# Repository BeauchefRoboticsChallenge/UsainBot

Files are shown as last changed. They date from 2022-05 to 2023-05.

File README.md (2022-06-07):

# UsainBot
[][cc-by-nc-sa]

UsainBot es un robot velocista del tipo seguidor de líneas cuyo objetivo es servir de referencia y plataforma para apoyar en la formación de los competidores. Está desarrollado en base a las tecnologías disponibles en un FabLab (impresión 3D, corte de PCBs, Arduino) y comprende las componentes más básicas para funcionar de acuerdo a las reglas de la competencia.

Un velocista seguidor de línea es un robot con ruedas que tiene la capacidad de distinguir franjas en una superficie de alto contraste (blanco y negro) y seguir su trayectoria de forma autónoma con la finalidad de completar un circuito lo más rápido posible.

# Diseño

## Antecedentes

Las funciones principales requeridas por el robot son:

- Reconocer franjas
- Movimiento
- Energía
- Procesamiento y control

Para esto requiere una construcción óptima en cuanto al tamaño/peso y las prestaciones de sus componentes que cumplirán estas funcionalidades, las cuales pueden ser desempeñadas por diferentes tipos y arreglos de sensores, motores, baterías, etc. Otras funciones secundarias corresponden a la interacción con el usuario (encender/apagar, activar, indicar acciones), así como cualquier otra que se desee agregar (como comunicación inalámbrica para el debugging).

En el contexto de la competencia, existirán marcadores a los costados del circuito que indicarán hitos como curvas, cruces y fin. También se fija el tamaño máximo como 25x25x20 centímetros (largo, ancho y alto) y que las ruedas no pueden contener elementos adherentes que dañen la pista.

(imagen de los hitos)

## Diseño original

UsainBot se diseñó considerando este set mínimo de subsistemas, las tecnologías disponibles en el Fablab U de Chile, la disponibilidad de componentes comerciales en el país (Chile) y otros diseños populares de robots velocistas. Los dibujos del sistema se realizaron en AutodeskFusion 360 y se llegó al siguiente diseño:

(vistas del usainbot)

### Sensores

UsainBot cuenta con un arreglo de sensores infrarrojos modelo asdasdasdsad en el frente. Esta disposición permite detectar con cierto nivel de resolución la desviación del eje central del robot respecto a la franja del circuito y tener un mejor control:

(esquema)

También posee dos sensores simples del mismo tipo (modelo sadads) en cada lado para la detección de franjas.

(imagen con zoom)

### Actuación

El robot posee una configuración diferencial, dos ruedas controladas por motores DC idénticos modelo asdasdsad, de x rpm nominales y v Volts.

La llanta de la rueda, impresa en 3D, posee una muesca donde se inserta el eje del motor (que tiene una muesca opuesta) a presión, mientras que el neumático es de silicona.

Los motores se apernan al chasis mediante soportes impresos en 3D.

Considerando la corriente que requieren estos motores elegimos utilizar como driver el puente H sadasdasdasd.

### Controlador

Decidimos utilizar un Arduino Nano por varias razones: Soporte de software, tamaño, lógica de 5V (compatible con el resto de componentes), disponibilidad, precio, facilidad de uso (cuenta con pines y puerto USB), entre otras.

### Batería

Considerando el voltaje necesario para el controlador y los motores, los cuales además suelen requerir altos niveles de corriente súbitamente es que elegimos utilizar una batería LiPo de 7.4 V modelo asdsdasad. Con tal capacidad permitirá realizar pruebas un par de horas antes de volver a cargarla sin conllevar mucho peso sobre el sistema.

### Chasis

Con el objetivo de minimizar el peso y tamaño se diseña una PCB con doble propósito: ubicar los componentes en el mínimo espacio posible y como chasis del robot, considerando que la placa de sadklsdajlkasdjlk tiene rigidez suficiente.

(imagen de la PCB)

La PCB tiene conectores para intercambiar fácilmente los componentes en caso de que sufran algún desperfecto, así como orificios para el montaje de los motores.

### Otros

Como tercer punto de apoyo se utiliza la parte cabeza de un LED redondo.

Utilizamos un buzzer standard de 5V para que el robot informe mediante alertas sonoras el estado en el que se encuentra.

Incluimos un switch para energizar los sistemas desde la batería y un pulsador para iniciar la rutina de carrera.

# Lista de partes y materiales

## Partes comerciales

Item                     | Cantidad
 ---------------------------   | --------------
Motor DC con reducción 6V x rpm | 2
Driver asdasd | 1
Sensor QTR-8A | 1
Sensor QTR-1A | 2
Arduino Nano | 1
Lipo 7.4V | 1
Pulsador | 1
Switch | 1
LED | 1
Buzzer | 1

Otros elementos necesarios para el desarrollo del robot pero no que son parte del mismo corresponden a: cargador de LiPo, alarma de carga de batería.

## Partes manufacturadas

Item                     | Cantidad
 ---------------------------   | ------------
Llantas | 2
Neumáticos | 2
Chasis PCB | 1

## Materiales

- pines, conectores,
- placa fr-4
- silicona epóxica 20-50 Shore A
- pernos m3x8 (4)
- tuerca m3 (4)

# Manufactura

## Componentes

### Llantas y neumáticos

Dado que tenemos acceso a una impresora de tipo SLA (Form2), decidimos fabricar las llantas con resina tenaz (Tough Resin) para soportar posibles golpes y el ajuste a presión sobre el eje, y moldes para los neumáticos con resina estándar translúcida (Clear Resin), pues de esta forma es fácil desprender la pieza moldeada del molde mismo y además permite observar la presencia de burbujas durante el procseo de curado.

El neumático se fabrica directamente sobre la llanta, como se muestra en el diagrama:

Para el proceso es necesario mezclar la silicona en partes iguales, revolver y degasificar rapidamente antes de que la silicona empiece a solidificarse.

### Anclajes de motor

Estos anclajes afirman el motor utilizando pernos M3x8 y tuercas M3, son impresos en FDM con PLA.

### PCB

Para la manufactura de la PCB contamos con una máquina LPKF modelo sadasdsda. Las herramientas que utilizamos para el corte son:

- sdaasd
- asdsd
- sadsdasadsda

Antes de empezar a soldar los componentes es importante probar la integridad de las pistas midiendo la conductividad con un multímetro, para evitar corto circuitos y circuitos abiertos.

Luego soldamos los pines, buzzer, pulsador, switch y LED de acuerdo al esquema.

## Ensamble

1.- Montar las ruedas en cada motor
2.- Montar los motores con sus anclajes sobre la PCB.
3.- Conectar Arduino Nano
4.- Conectar sensores laterales
5.- Conectar arreglo de sensores frontal.
6.- Conectar driver.
7.- Montar batería con un elástico y conectar.

# Software

## Pista de pruebas

Para hacer pruebas de funcionamiento resulta muy útil tener una pequeña pista de pruebas, esta la fabricamos con un trozo de melamina delgado de color negro y cinta aislante de x mm de ancho de color blanco.

(imagen de la pista)

## Pruebas de subsistemas

Una vez que el sistema está ensamblado, los componentes deben ser probados separadamente antes de hacer la integración final. Para esto generamos códigos sencillos para ejecutar en el robot y observar tanto su funcionamiento como la información que entrega el Arduino a través del monitor serial.

- Prueba de motores.
- Prueba de sensores principal.
- Prueba de sensores laterales.

(links a los codigos)

## Integración

## Calibración del PID

El funcionamiento óptimo del robot implica maximizar la velocidad manteniendo el robot moviéndose dentro de la franja y colineal con esta. Para esto es necesario encontrar una configuración óptima de los parámetros del PID.

### Calibración "manual"

De acuerdo al comportamiento observado en las pruebas, se pueden hacer las siguientes modificaciones:

## Licencia
[][cc-by-nc-sa]

Este trabajo esta publicado bajo la licencia [Creative Commons Attribution-NonCommercial-ShareAlike 4.0 International
License][cc-by-nc-sa].

Si deseas utilizar nuestro robot en tus proyectos o si te interesa vender las placas, contáctanos y conversemos :)

[cc-by-nc-sa]: https://creativecommons.org/licenses/by-nc-sa/4.0/
[cc-by-nc-sa-image]: https://i.creativecommons.org/l/by-nc-sa/4.0/88x31.png
[cc-by-nc-sa-shield]: https://img.shields.io/badge/License-CC%20BY%20NC%20SA%204.0-lightgrey.svg

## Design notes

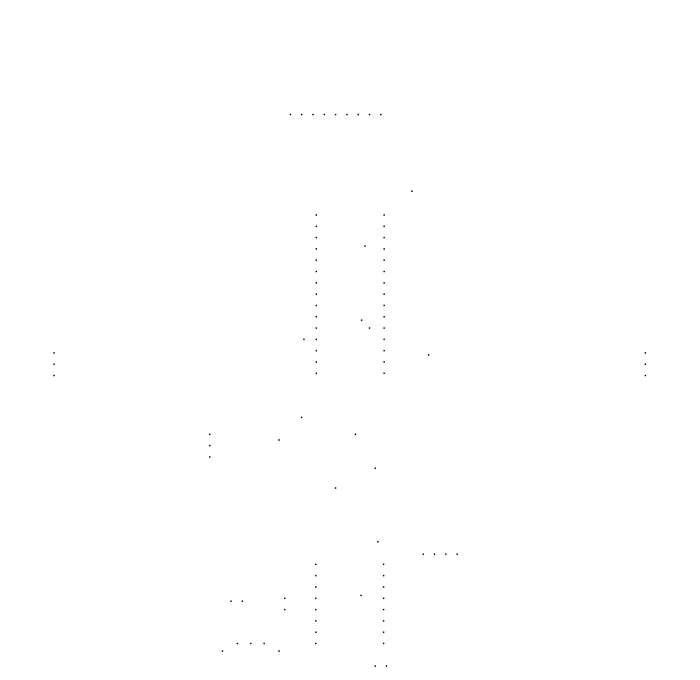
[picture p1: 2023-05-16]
pcb/usainbot2/usainv3_fabmod/drills.png

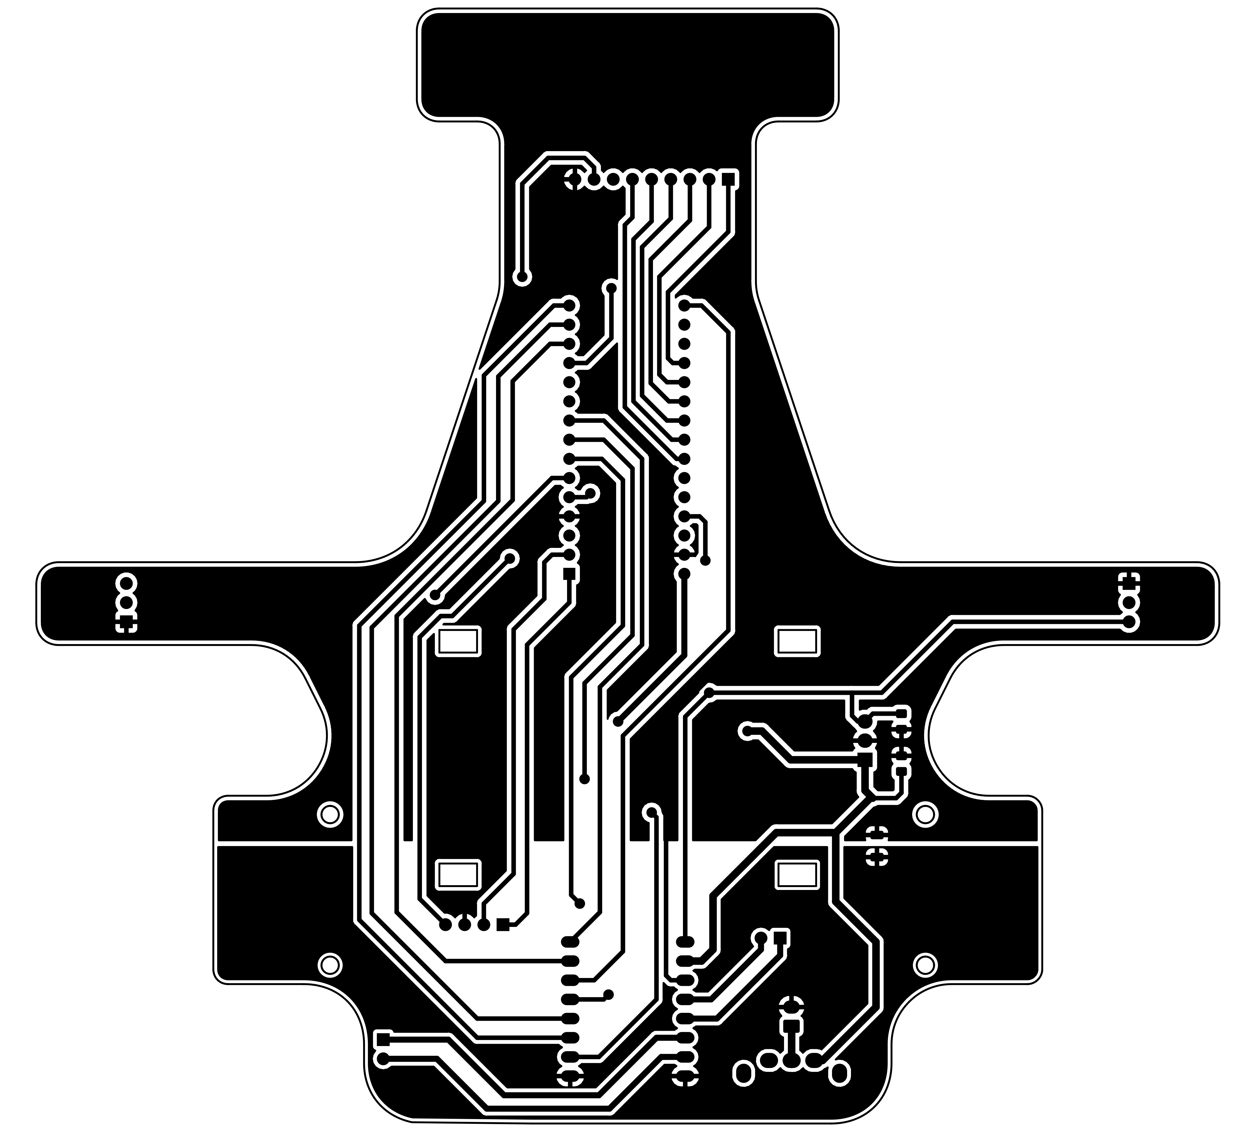
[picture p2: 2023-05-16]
pcb/usainbot2/brcito_fabmod/bot_inverted.png

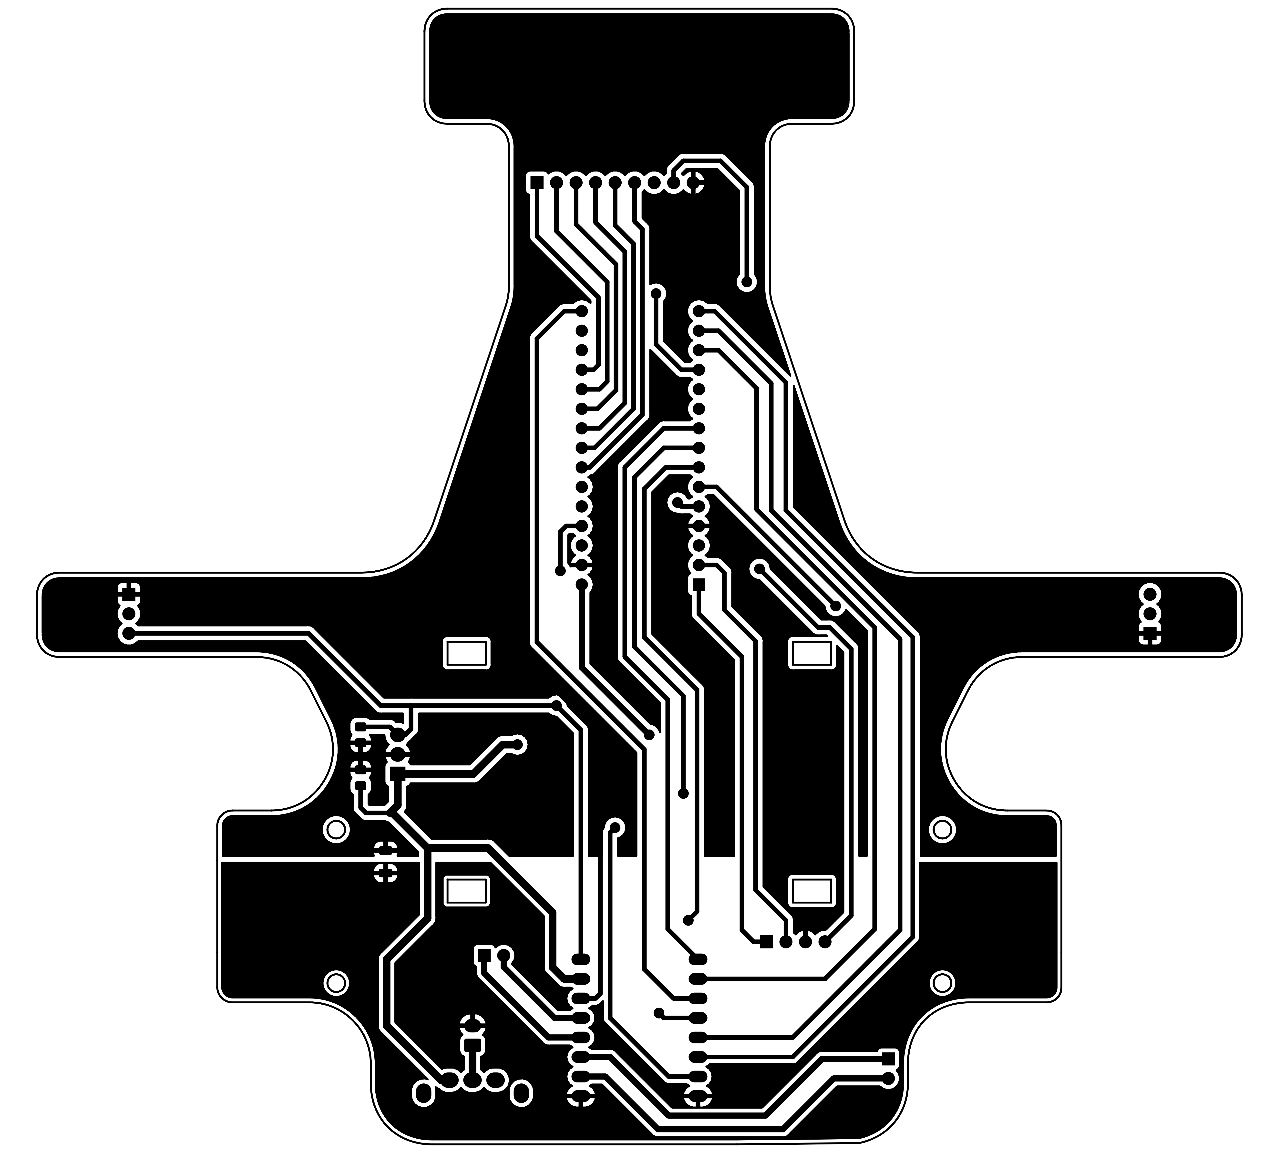
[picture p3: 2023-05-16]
pcb/usainbot2/brcito_fabmod/bot.png

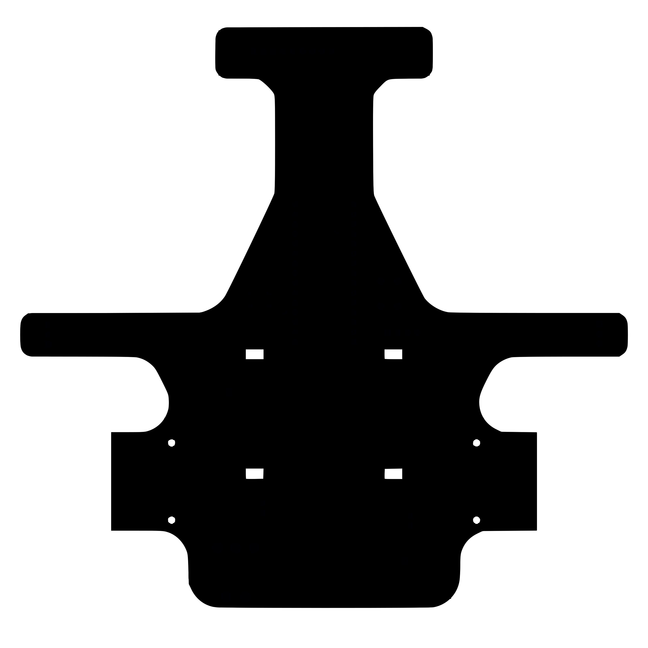
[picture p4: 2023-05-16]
pcb/usainbot2/contorno.png

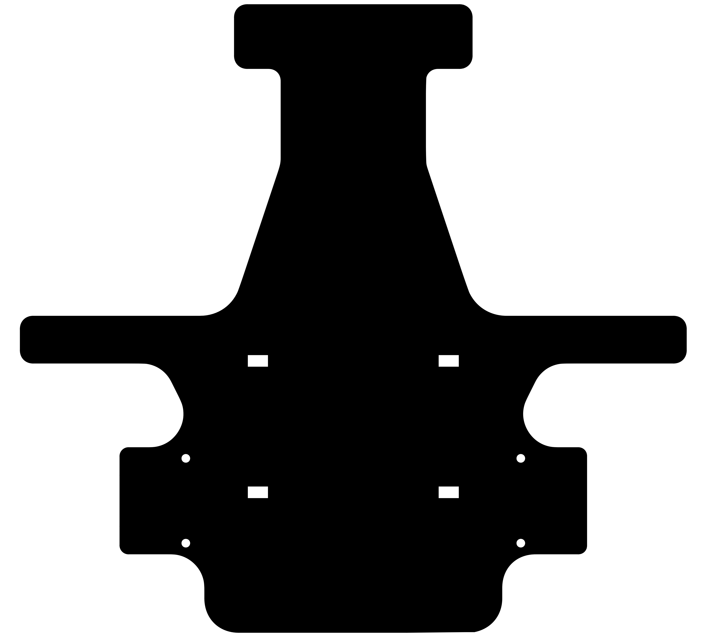
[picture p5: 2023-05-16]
pcb/usainbot2/brcito_fabmod/contorno.png

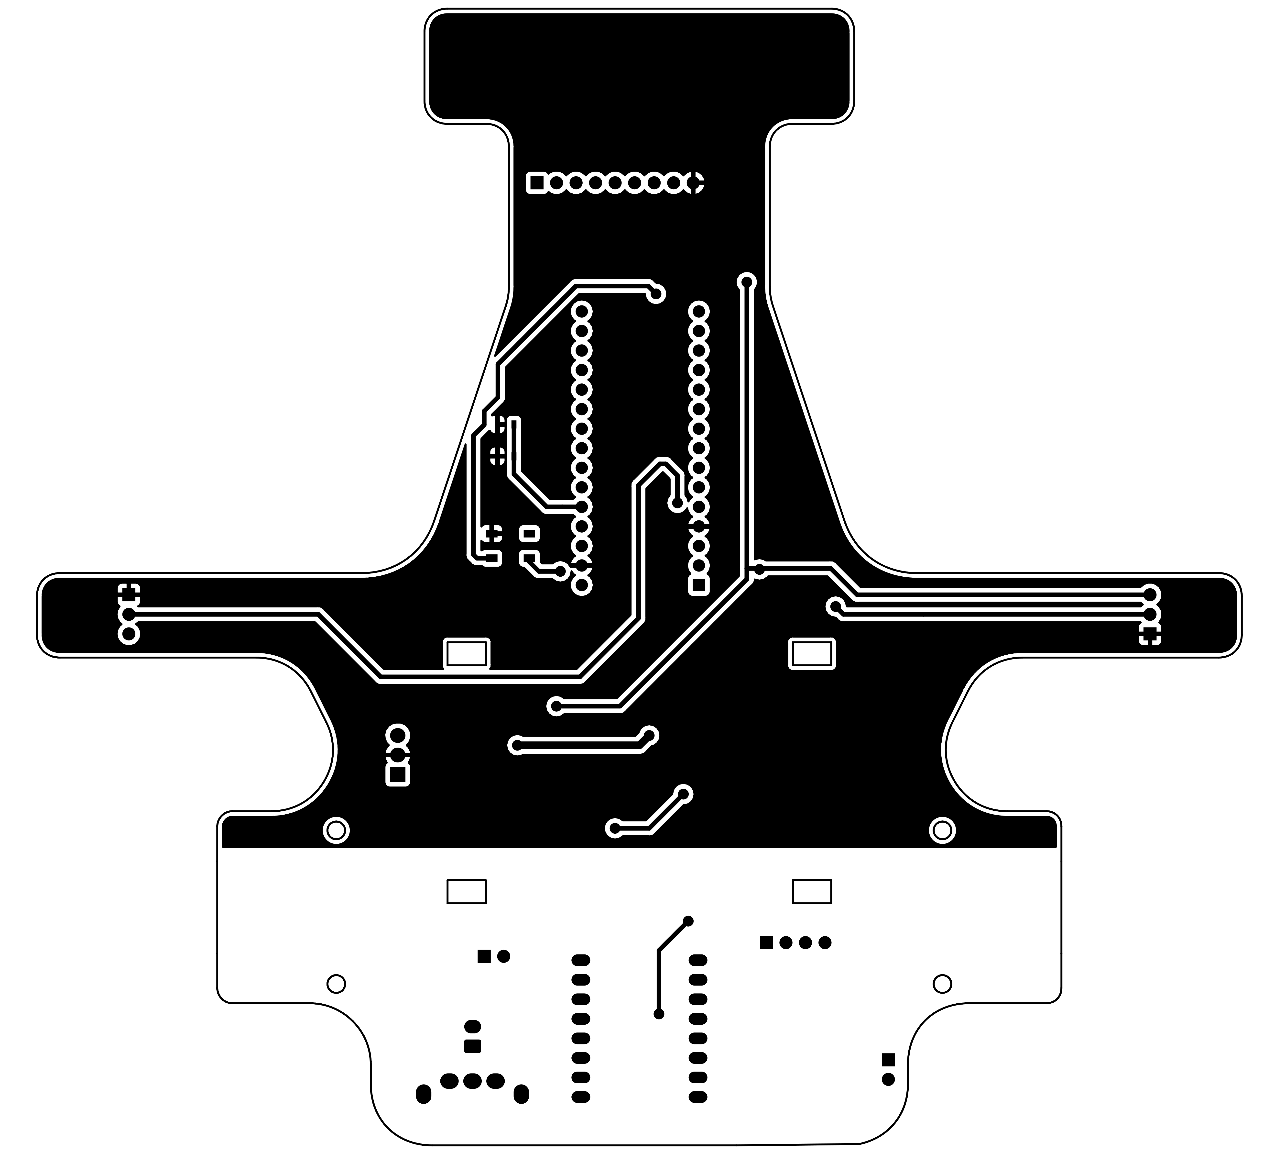
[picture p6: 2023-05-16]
pcb/usainbot2/brcito_fabmod/top.png

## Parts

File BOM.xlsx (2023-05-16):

Id | Designator | Package | Quantity | Designation | Supplier and ref
1 | U1 | TB6612FNG Breakout | 1 | TB6612FNG_breakout
 |  |  | 2 | pin socket 8x1
2 | J1 | PinSocket_1x04_P2.54mm_Vertical | 1 | BT_MOD
 |  |  | 1 | pin socket 4x1
3 | ArduinoNano1 | Arduino_Nano | 1 | Arduino_Nano_v3.x
 |  |  | 2 | pin socket 15x1
4 | C3,C2,C4 | C_0805_2012Metric_Pad1.18x1.45mm_HandSolder | 3 | 0.1u
5 | J5 | Molex_KK-254_AE-6410-06A_1x06_P2.54mm_Vertical | 1 | M1
6 | D1,D2 | LED_WS2812B_PLCC4_5.0x5.0mm_P3.2mm | 2 | WS2812B
7 | SW1 | SPST slide switch | 1 | SW_SPDT
8 | SW2 | SW_Push_1P1T_NO_Vertical_Wuerth_434133025816 | 1 | SW_Push
9 | U2 | TO-220-3_Vertical | 1 | LM7805_TO220
 |  |  | 1 | pin socket 3x1
10 | J7 | Molex_KK-254_AE-6410-06A_1x06_P2.54mm_Vertical | 1 | M2
11 | J6 | Molex_KK-254_AE-6410-02A_1x02_P2.54mm_Vertical | 1 | BATT
12 | J4 | PinHeader_1x09_P2.54mm_Horizontal | 1 | QTR-6A
13 | J3 | PinHeader_1x03_P2.54mm_Vertical | 1 | QTR1-R
14 | R0 | R_1206_3216Metric | 1 | RESISTOR1206
15 | J2 | PinHeader_1x03_P2.54mm_Vertical | 1 | QTR1-L
16 | R1 | R_1206_3216Metric_Pad1.30x1.75mm_HandSolder | 1 | 1K
17 | R2 | R_1206_3216Metric_Pad1.30x1.75mm_HandSolder | 1 | 2K
18 | C1 | C_0805_2012Metric_Pad1.18x1.45mm_HandSolder | 1 | 0.22u

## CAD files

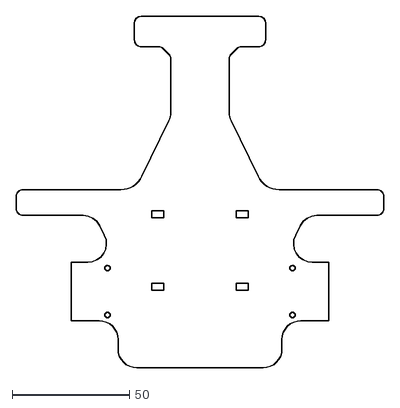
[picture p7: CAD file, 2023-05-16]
pcb/usainbot2/Maggibot_2022.dxf
157.0 x 150.0

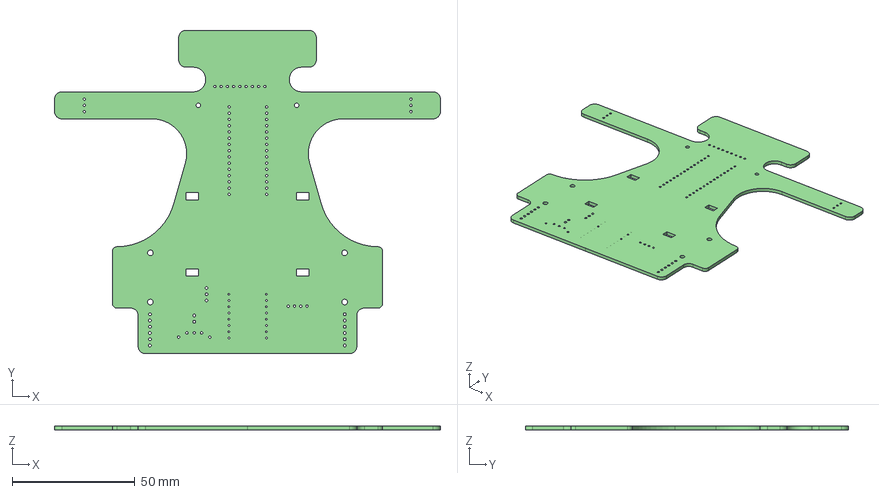
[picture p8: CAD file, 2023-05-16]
pcb/usainbot2/usainv3_fabmod/usainbot3.step
157.0 x 131.5 x 1.60 mm

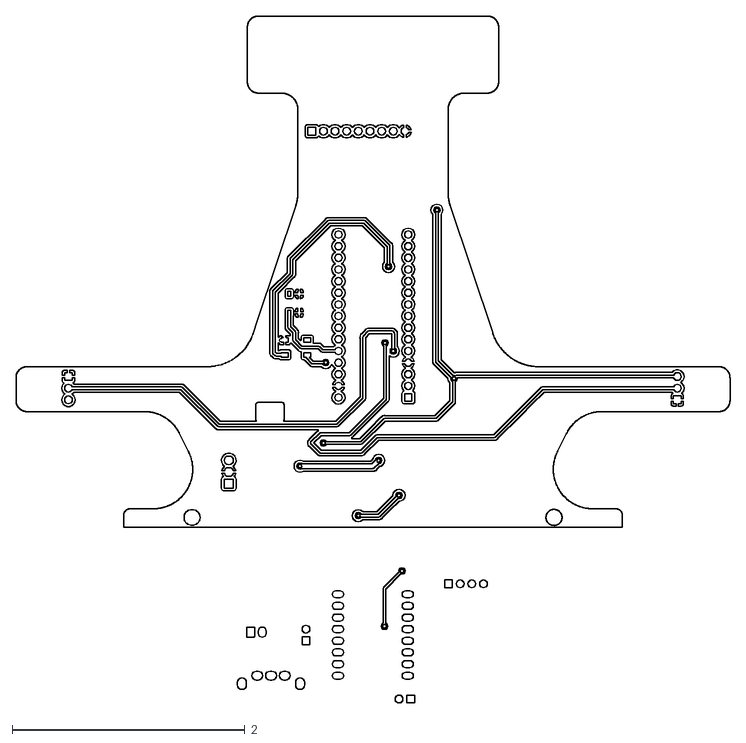
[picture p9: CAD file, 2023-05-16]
pcb/usainbot2/usainbot2-F_Cu.dxf
6.13 x 5.90

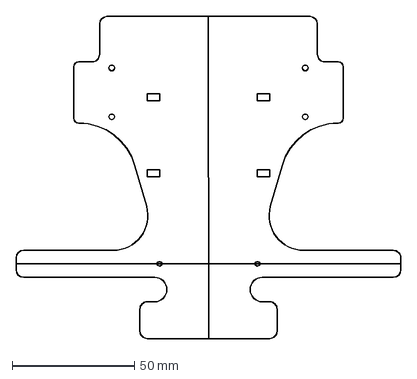
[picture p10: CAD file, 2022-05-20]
pcb/usainbot2/usainbot21_outline.dxf
157.0 x 131.5 mm

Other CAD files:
pcb/usainbot2/usainbot2.step

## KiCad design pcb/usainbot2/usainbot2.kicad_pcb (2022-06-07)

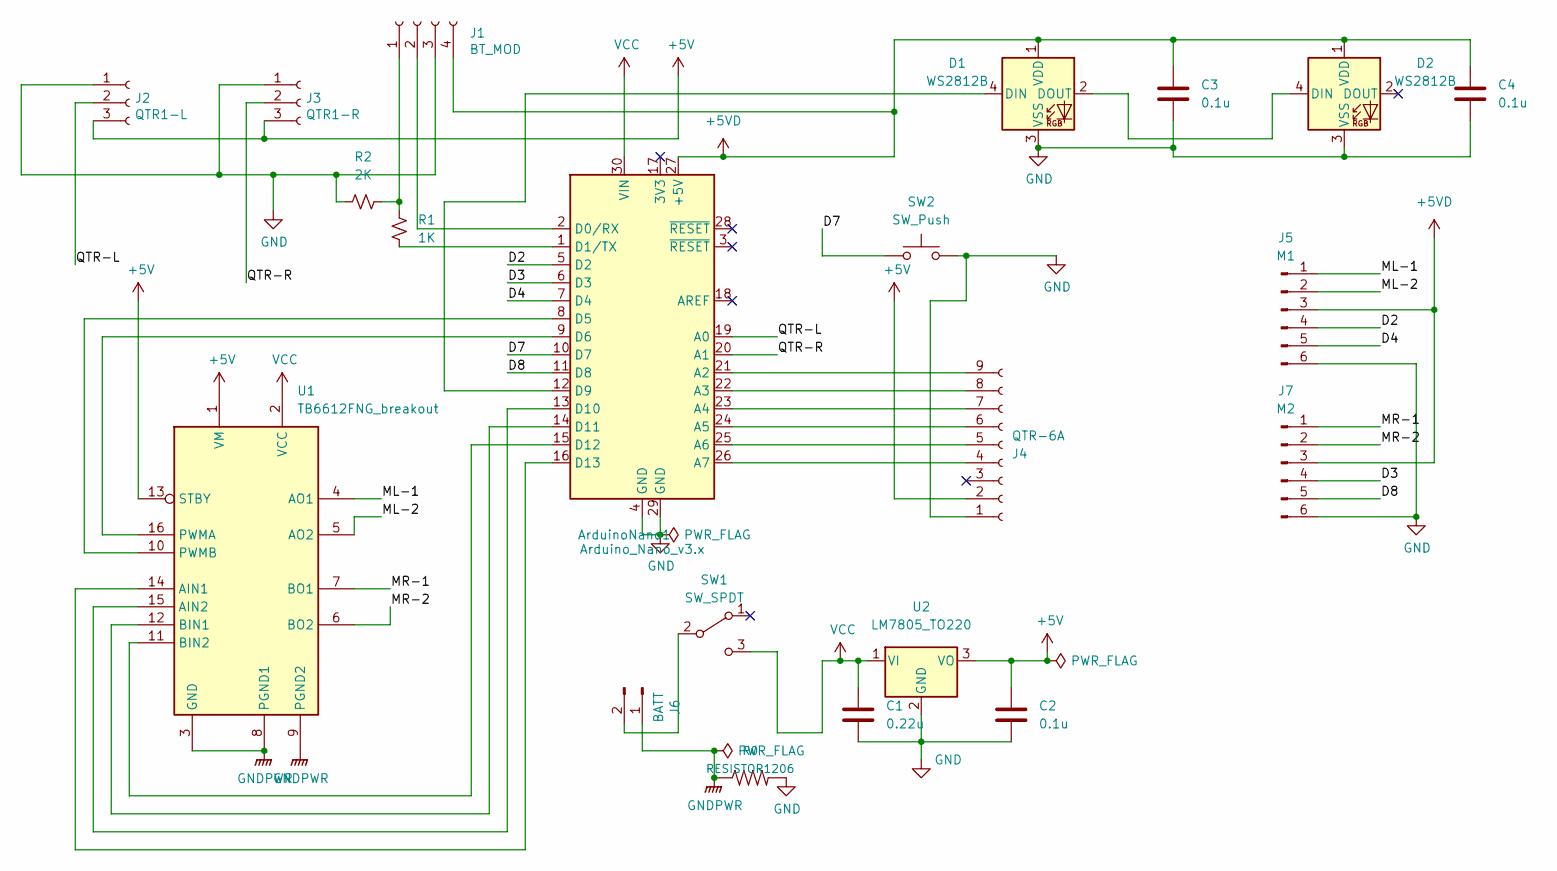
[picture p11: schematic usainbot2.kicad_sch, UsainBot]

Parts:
ArduinoNano1: Arduino_Nano_v3.x; Arduino_Nano
C1: 0.22u; C_0805_2012Metric_Pad1.18x1.45mm_HandSolder
C2, C3, C4: 0.1u; C_0805_2012Metric_Pad1.18x1.45mm_HandSolder
D1, D2: WS2812B; LED_WS2812B_PLCC4_5.0x5.0mm_P3.2mm
J1: BT_MOD; PinSocket_1x04_P2.54mm_Vertical
J2: QTR1-L; PinHeader_1x03_P2.54mm_Vertical
J3: QTR1-R; PinHeader_1x03_P2.54mm_Vertical
J4: QTR-6A; PinHeader_1x09_P2.54mm_Horizontal
J5: M1; Molex_KK-254_AE-6410-06A_1x06_P2.54mm_Vertical
J6: BATT; Molex_KK-254_AE-6410-02A_1x02_P2.54mm_Vertical
J7: M2; Molex_KK-254_AE-6410-06A_1x06_P2.54mm_Vertical
R0: RESISTOR1206; R_1206_3216Metric
R1: 1K; R_1206_3216Metric_Pad1.30x1.75mm_HandSolder
R2: 2K; R_1206_3216Metric_Pad1.30x1.75mm_HandSolder
SW1: SW_SPDT; SPST slide switch
SW2: SW_Push; SW_Push_1P1T_NO_Vertical_Wuerth_434133025816
U1: TB6612FNG_breakout; TB6612FNG Breakout
U2: LM7805_TO220; TO-220-3_Vertical

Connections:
+5V: C2.1, J2.3, J3.3, J4.2, U1.1 (VM), U1.13 (STBY), U2.3 (VO)
+5VD: ArduinoNano1.27 (+5V), C3.1, C4.1, D1.1 (VDD), D2.1 (VDD), J1.4, J5.3, J7.3
/D2: ArduinoNano1.5 (D2), J5.4
/D3: ArduinoNano1.6 (D3), J7.4
/D4: ArduinoNano1.7 (D4), J5.5
/D7: ArduinoNano1.10 (D7), SW2.1
/D8: ArduinoNano1.11 (D8), J7.5
/ML-1: J5.1, U1.4 (AO1)
/ML-2: J5.2, U1.5 (AO2)
/MR-1: J7.1, U1.7 (BO1)
/MR-2: J7.2, U1.6 (BO2)
/QTR-L: ArduinoNano1.19 (A0), J2.2
/QTR-R: ArduinoNano1.20 (A1), J3.2
GND: ArduinoNano1.4 (GND), ArduinoNano1.29 (GND), C1.2, C2.2, C3.2, C4.2, D1.3 (VSS), D2.3 (VSS), J1.3, J2.1, J3.1, J4.1, J5.6, J7.6, R0.2, R2.2, SW2.2, U2.2 (GND)
GNDPWR: J6.1, R0.1, U1.3 (GND), U1.8 (PGND1), U1.9 (PGND2)
unnamed: ArduinoNano1.1 (D1/TX), R1.2
unnamed: ArduinoNano1.2 (D0/RX), J1.2
unnamed: ArduinoNano1.8 (D5), U1.10 (PWMB)
unnamed: ArduinoNano1.9 (D6), U1.16 (PWMA)
unnamed: ArduinoNano1.12 (D9), D1.4 (DIN)
unnamed: ArduinoNano1.13 (D10), U1.15 (AIN2)
unnamed: ArduinoNano1.14 (D11), U1.12 (BIN1)
unnamed: ArduinoNano1.15 (D12), U1.11 (BIN2)
unnamed: ArduinoNano1.16 (D13), U1.14 (AIN1)
unnamed: ArduinoNano1.21 (A2), J4.9
unnamed: ArduinoNano1.22 (A3), J4.8
unnamed: ArduinoNano1.23 (A4), J4.7
unnamed: ArduinoNano1.24 (A5), J4.6
unnamed: ArduinoNano1.25 (A6), J4.5
unnamed: ArduinoNano1.26 (A7), J4.4
unnamed: D1.2 (DOUT), D2.4 (DIN)
unnamed: J1.1, R1.1, R2.1
unnamed: J6.2, SW1.2 (B)
VCC: ArduinoNano1.30 (VIN), C1.1, SW1.3 (C), U1.2 (VCC), U2.1 (VI)

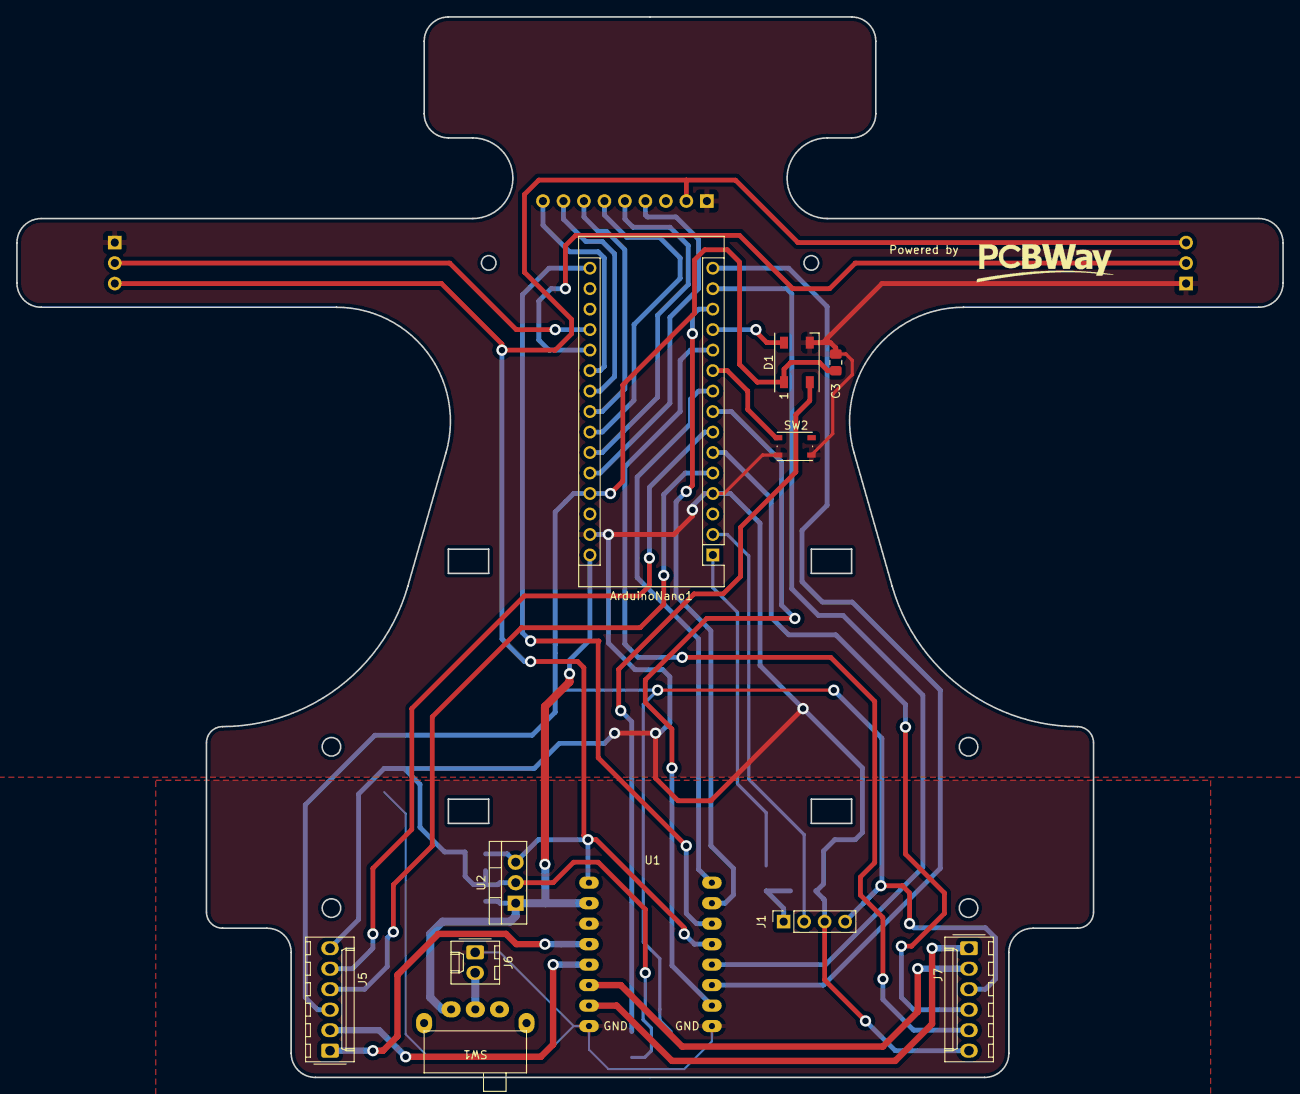
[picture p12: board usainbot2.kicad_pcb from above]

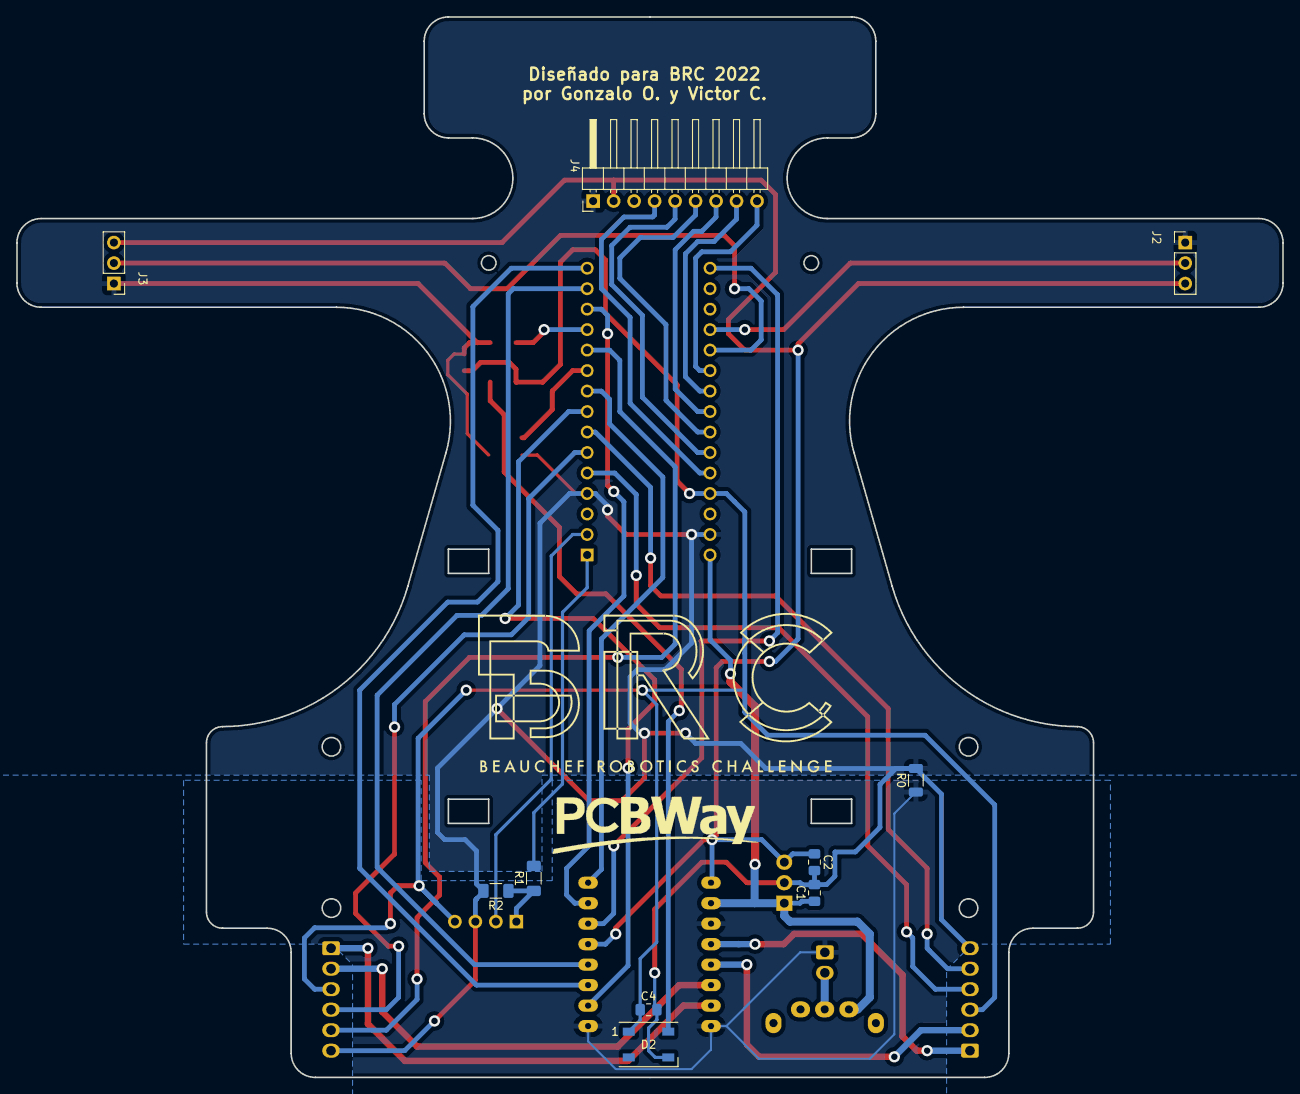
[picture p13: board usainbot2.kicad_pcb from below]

Board: 2 copper layers, 157.0 x 131.5 mm, 21 parts (10 on the bottom side), 34 nets.

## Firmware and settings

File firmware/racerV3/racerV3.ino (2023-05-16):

/* Sketch UsainBot v2.0

   by Gonzalo Olave based on v1.0 by Matias Mattamala and G.O.
   v1.0 -> https://github.com/mmattamala/racer/blob/master/arduino/robot_brc/robot_brc.ino
   last update 26/4/2022

   This code is in the public domain and it is licensed under the BEER-JUICE-WARE licence

   ------------------------------------------------------------
   "THE BEERWARE LICENSE" (Revision 42):
   The authors wrote this code. As long as you retain this
   notice, you can do whatever you want with this stuff. If we
   meet someday, and you think this stuff is worth it, you can
   buy us a beer in return (or a juice).
   ------------------------------------------------------------
*/

// debug
//#define DEBUG_SENSORS

#define CALIBRATE
// serial debug
#define DEBUG

#define LINE_WHITE

#include "DebugUtils.h"
#include <Adafruit_NeoPixel.h>
#include <QTRSensors.h>

// pinout del robot
#include "BRCito_defines.h"

// General definitions
#define LW 0  // left wheel
#define RW 1  // right wheel

#define TIMEOUT 2500

// Estos valores definen las velocidades de las ruedas
#define VEL_MIN 220
#define VEL_MAX 240        //130
#define VEL_CURVA_MAX 230  // 110
#define VEL_CURVA_MIN 0
#define MIN_ERR_THR 1000

// parámetros del controlador PID, para motores pololu de 1000rpm KP<1
float KP = 3;  // 0.3 //2
float KI = 0;
float KD = 15;  //5

// side sensor threshold
#define RS_TH 500
#define LS_TH 500

int r_sensor = 0;
int l_sensor = 0;
int r_counter = 0;
int l_counter = 0;
int st_sensor = 0;

float prop_err, int_err, der_err, last_err;
float pid_out;

bool stdby_state = 0;

// Variables will change:
int idleState = HIGH;       // the current state of the robot
int buttonState;            // the current reading from the input pin
int lastButtonState = LOW;  // the previous reading from the input pin

// the following variables are unsigned longs because the time, measured in
// milliseconds, will quickly become a bigger number than can be stored in an int.
unsigned long lastDebounceTime = 0;  // the last time the output pin was toggled
unsigned long debounceDelay = 50;    // the debounce time; increase if the output flickers

uint8_t lw_speed;
uint8_t rw_speed;

int th = 800;
float sum1 = 0;
float sum = 0;
float err = 0;
int s_min = TIMEOUT;
int s_max = 0;
float pos = 0;

int counter = 0;
int btn = 0;

uint16_t sensorSide[NUM_SIDE_SENSORS];
uint16_t sensorLine[NUM_ARRAY_SENSORS];

Adafruit_NeoPixel pixel = Adafruit_NeoPixel(2, LED_PIN, NEO_GRB + NEO_KHZ800);
QTRSensors qtr_line, qtr_side;

uint32_t BLACK = pixel.Color(0, 0, 0);
uint32_t RED = pixel.Color(255, 0, 0);        // rojo
uint32_t GREEN = pixel.Color(0, 255, 0);      // magenta
uint32_t BLUE = pixel.Color(0, 0, 200);       // magenta
uint32_t MAGENTA = pixel.Color(255, 0, 200);  // magenta
uint32_t YELLOW = pixel.Color(255, 140, 0);   // magenta
uint32_t ORANGE = pixel.Color(255, 50, 0);    // magenta
uint32_t CYAN = pixel.Color(0, 140, 200);     // cyan

int state = STDBY;

//-------------------------------
// Setup functions
//-------------------------------
void setupWheels() {

  // configure left wheel
  pinMode(PIN_LW_PWM, OUTPUT);
  pinMode(PIN_LW_A, OUTPUT);
  pinMode(PIN_LW_B, OUTPUT);

  // configure right wheel
  pinMode(PIN_RW_PWM, OUTPUT);
  pinMode(PIN_RW_A, OUTPUT);
  pinMode(PIN_RW_B, OUTPUT);

  onWheels();
}

void setupHW() {
  pinMode(BUTTON_PIN, INPUT_PULLUP);
}

void setupLeds() {
  pixel.begin();
}

void setupSensors() {
  qtr_side.setTypeRC();
  qtr_side.setSensorPins((const uint8_t[]){
                           PIN_LS, PIN_RS },
                         NUM_SIDE_SENSORS);
  qtr_line.setTypeAnalog();
  qtr_line.setSensorPins((const uint8_t[]){
    S1, S2, S3, S4, S5, S6}, NUM_ARRAY_SENSORS);

#ifdef CALIBRATE
  pixel.setPixelColor(LED_UP, RED);
  pixel.show();
  DEBUG_PRINT("Calibrando...");
  for (int i = 0; i < 100; i++)  // make the calibration take about 10 seconds
  {
    qtr_line.calibrate();
    qtr_side.calibrate();
  }
  pixel.setPixelColor(0, BLACK);
  pixel.show();
  DEBUG_PRINTLN("ok");
#endif
}

void setup() {

  Serial.begin(115200);  // for BT communication and debug

  setupWheels();
  setupLeds();
  setupHW();
  setupSensors();

  delay(500);

  pixel.setBrightness(100);
  pixel.setPixelColor(LED_UP, YELLOW);
  pixel.show();
  delay(500);

  while (true) {
    int boton = digitalRead(BUTTON_PIN);
    if (boton == 0) break;
  }
  delay(100);

  pixel.setPixelColor(LED_UP, GREEN);
  pixel.show();

  pixel.setPixelColor(LED_DOWN, BLUE);
  pixel.show();
  state = FOLLOW_LINE;
}

void loop() {
  // Step 1: Read Raw Sensors
  readRawSensors();

  //testBlink();
  /*
    testWheel(RW);
    delay(1000);
    testWheel(LW);
    delay(1000);
    handBrake();
  */

  btn = digitalRead(BUTTON_PIN);
  debounceButton();

  //DEBUG_PRINTLN(btn);

  if (idleState == LOW) {
    onWheels();
    lineFollowing();
    if (l_sensor < LS_TH) {
      l_counter++;
      pixel.setPixelColor(LED_UP, GREEN);
      pixel.show();
    } else if (r_sensor < RS_TH) {
      r_counter++;
      pixel.setPixelColor(LED_UP, ORANGE);
      pixel.show();
    } else {
      pixel.setPixelColor(LED_UP, BLACK);
      pixel.setPixelColor(LED_DOWN, BLUE);
      pixel.show();
    }
    if (l_sensor < LS_TH && r_sensor < RS_TH) {
      pixel.setPixelColor(LED_UP, BLUE);
      pixel.show();
    }
  } else if (idleState == HIGH) {
    pixel.setPixelColor(LED_UP, RED);
    pixel.setPixelColor(LED_DOWN, RED);
    pixel.show();
    handBrake();
  }
  lastButtonState = btn;
}

void debounceButton() {
  // If the switch changed, due to noise or pressing:
  if (btn != lastButtonState) {
    // reset the debouncing timer
    lastDebounceTime = millis();
  }
  if ((millis() - lastDebounceTime) > debounceDelay) {
    // whatever the reading is at, it's been there for longer than the debounce
    // delay, so take it as the actual current state:

    // if the button state has changed:
    if (btn != buttonState) {
      buttonState = btn;

      // only toggle the LED if the new button state is HIGH
      if (buttonState == HIGH) {
        idleState = !idleState;
      }
    }
  }
}

//-------------------------------
// Line following functions
//-------------------------------

void lineFollowing() {
  // Step 1: Read Raw Sensors
  // readRawSensors(); -> se lee en el inicio del loop
  // Step 2: Compute error
  computeError();
  // Step 3: Compute PID correction
  computePID();
  // Step 4: Map error correction to motor speeds
  computeMotorSpeeds();
  // Step 5: Apply speeds
  setMotorSpeeds();
}

void readRawSensors() {

  qtr_line.readCalibrated(sensorLine);
  qtr_side.readCalibrated(sensorSide);

#ifdef LINE_WHITE
  pos = qtr_line.readLineWhite(sensorLine);
#else
  pos = qtr_line.readLineBlack(sensorLine);
#endif

  l_sensor = sensorSide[0];
  r_sensor = sensorSide[1];

#ifdef DEBUG_SENSORS
  for (uint8_t i = 0; i < 6; i++) {
    Serial.print(sensorLine[i]);
    Serial.print('\t');
  }
  for (uint8_t i = 0; i < 2; i++) {
    Serial.print(sensorSide[i]);
    Serial.print('\t');
  }
  Serial.println();
#endif
  //DEBUG_PRINTLN(pos);
  //DEBUG_PRINTLN(l_sensor);
  DEBUG_PRINTLN(r_sensor);
}

void computeError() {
  prop_err = pos - TIMEOUT;
  der_err = prop_err - last_err;
  int_err += prop_err;

  last_err = prop_err;
  sum1 = 0;
  sum = 0;
}

void computePID() {
  pid_out = prop_err * KP + int_err * KI + der_err * KD;
  pid_out = pid_out > 2500 ? 2500 : (pid_out < (-2500) ? -2500 : pid_out);
  // DEBUG_PRINTLN(pid_out);
}

void computeMotorSpeeds() {

  if (pid_out > MIN_ERR_THR) {
    lw_speed = map(pid_out, -2500, 2500, VEL_CURVA_MIN, VEL_CURVA_MAX);
    rw_speed = VEL_CURVA_MIN;

  } else if (pid_out < -MIN_ERR_THR) {
    lw_speed = VEL_CURVA_MIN;
    rw_speed = map(pid_out, -2500, 2500, VEL_CURVA_MAX, VEL_CURVA_MIN);

  } else {
    int diff = VEL_MAX - VEL_MIN;
    rw_speed = VEL_MIN + map(pid_out, -MIN_ERR_THR, MIN_ERR_THR, -diff, diff);
    lw_speed = VEL_MIN + map(pid_out, -MIN_ERR_THR, MIN_ERR_THR, diff, -diff);
  }
}


void setMotorSpeeds() {
  analogWrite(PIN_LW_PWM, lw_speed);
  analogWrite(PIN_RW_PWM, rw_speed);
}

void handBrakeLeft() {
  analogWrite(PIN_LW_PWM, 0);
  digitalWrite(PIN_LW_A, HIGH);
  digitalWrite(PIN_LW_B, HIGH);
}

void handBrakeRight() {
  analogWrite(PIN_RW_PWM, 0);
  digitalWrite(PIN_RW_A, HIGH);
  digitalWrite(PIN_RW_B, HIGH);
}

void handBrake() {
  handBrakeLeft();
  handBrakeRight();
}

void onWheels() {
  // this depends on motor connections to driver
  digitalWrite(PIN_LW_A, HIGH);
  digitalWrite(PIN_LW_B, LOW);

  digitalWrite(PIN_RW_A, LOW);
  digitalWrite(PIN_RW_B, HIGH);
}



//-------------------------------
// Test functions
//-------------------------------
void testBlink() {
  /*
    uint32_t color = pixel.Color(255,0,255); // magenta
    pixel.setPixelColor(0,color);
    pixel.show();
  */
  PlasmaPulse(30);
}

void testWheel(int wheel) {

  int t = 20;
  if (wheel == RW) {
    for (int i = 0; i < 255; i += 5) {
      analogWrite(PIN_RW_PWM, i);
      Serial.println("Testing " + String(wheel == LW ? "left " : "right") + " wheel, power = " + String(i));
      delay(t);
    }
    for (int i = 255; i > 0; i -= 5) {
      analogWrite(PIN_RW_PWM, i);
      Serial.println("Testing " + String(wheel == LW ? "left " : "right") + " wheel, power = " + String(i));
      delay(t);
    }
  } else if (wheel == LW) {
    for (int i = 0; i < 255; i += 5) {
      analogWrite(PIN_LW_PWM, i);
      Serial.println("Testing " + String(wheel == LW ? "left " : "right") + " wheel, power = " + String(i));
      delay(t);
    }
    for (int i = 255; i > 0; i -= 5) {
      analogWrite(PIN_LW_PWM, i);
      Serial.println("Testing " + String(wheel == LW ? "left " : "right") + " wheel, power = " + String(i));
      delay(t);
    }
  }
}

void testBrake() {

  digitalWrite(PIN_RW_A, HIGH);
  digitalWrite(PIN_RW_B, LOW);
  digitalWrite(PIN_LW_A, HIGH);
  digitalWrite(PIN_LW_B, LOW);
  analogWrite(PIN_RW_PWM, 100);
  analogWrite(PIN_LW_PWM, 100);

  delay(2000);
  handBrake();

  delay(1000);
}

void PlasmaPulse(uint8_t wait) {
  uint16_t i, j;
  uint8_t brightness = 10;

  for (i = 0; i < pixel.numPixels(); i++) {
    pixel.setPixelColor(i, pixel.Color(255, 255, 255));
  }
  pixel.show();
  delay(wait);
  //Adjust 60 and 90 to the starting and ending colors you want to fade between.
  for (j = 170; j >= 135; --j) {
    for (i = 0; i < pixel.numPixels(); i++) {
      pixel.setPixelColor(i, Wheel((i + j) & 255));
    }
    pixel.show();
    brightness -= 6;
    pixel.setBrightness(brightness);
    delay(wait);
  }

  for (j = 135; j < 1170; j++) {
    for (i = 0; i < pixel.numPixels(); i++) {
      pixel.setPixelColor(i, Wheel((i + j) & 255));
    }
    pixel.show();
    brightness += 6;
    pixel.setBrightness(brightness);
    delay(wait);
  }

  for (i = 0; i < pixel.numPixels(); i++) {
    pixel.setPixelColor(i, pixel.Color(255, 255, 255));
  }
  pixel.show();
  delay(wait);
}

// Input a value 0 to 255 to get a color value.
// The colours are a transition r - g - b - back to r.
uint32_t Wheel(byte WheelPos) {
  if (WheelPos < 85) {
    return pixel.Color(WheelPos * 3, 255 - WheelPos * 3, 0);
  } else if (WheelPos < 170) {
    WheelPos -= 85;
    return pixel.Color(255 - WheelPos * 3, 0, WheelPos * 3);
  } else {
    WheelPos -= 170;
    return pixel.Color(0, WheelPos * 3, 255 - WheelPos * 3);
  }
}

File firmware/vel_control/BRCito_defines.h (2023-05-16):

// Wheel pins
// Left wheel (LW)
#define PIN_LW_PWM 6
#define PIN_LW_A 13
#define PIN_LW_B 10

#define LW_C1 2
#define LW_C2 4

// Right wheel (RW)
#define PIN_RW_PWM 5
#define PIN_RW_A 11
#define PIN_RW_B 12

#define RW_C1 3
#define RW_C2 8

// Sensor array
#define S1 A2
#define S2 A3
#define S3 A4
#define S4 A5
#define S5 A6
#define S6 A7

#define NUM_ARRAY_SENSORS 6
#define NUM_SIDE_SENSORS 2

// Right sensor
#define PIN_RS A1
// Left sensor
#define PIN_LS A0

#define LED_PIN 9
#define BUTTON_PIN 7

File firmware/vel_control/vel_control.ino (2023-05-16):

// pinout del robot
#include "BRCito_defines.h"

// General definitions
#define LW 0 // left wheel
#define RW 1 // right wheel

// Estos valores definen las velocidades de las ruedas
#define VEL_MIN 0
#define VEL_MAX 250//130
#define VEL_CURVA 230 // 110
#define MIN_ERR_THR 150 // mayor error 

long LW_counter=0,RW_counter=0;

void setup() {

  Serial.begin(115200);
  attachInterrupt(digitalPinToInterrupt(RW_C1), RW_ISR, RISING);
  attachInterrupt(digitalPinToInterrupt(LW_C1), LW_ISR, RISING);
}

void loop() {
  // put your main code here, to run repeatedly:
  Serial.print("LW: ");
  Serial.print(LW_counter);
  Serial.print("\tRW: ");
  Serial.println(RW_counter);
  
  delay(10);
}

void LW_ISR(){
  int8_t lwc2 = digitalRead(LW_C2);
  LW_counter += lwc2 ? 1 : -1;
}

void RW_ISR(){
  int8_t rwc2 = digitalRead(RW_C2);
  RW_counter += rwc2 ? -1 : 1;
}

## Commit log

2022-03-31 add board and gitignore
    [usainbot2.kicad_pcb, usainbot2.kicad_sch]
2022-04-13 update pcb, falta rutear
    [usainbot2.kicad_pcb, usainbot2.kicad_sch]
2022-04-19 sv with layers for milling
2022-04-19 last pcb update
    [usainbot2.kicad_pcb, usainbot2.kicad_sch]
2022-05-20 robot racer v2.1 kicad
    [usainbot2.kicad_pcb, usainbot2.kicad_sch]
2022-05-20 add power switch footprint
2022-05-20 add outline final dxf
    [usainbot21_outline.dxf]
2022-05-23 add led and add top pwrgnd isolation copper
    [usainbot2.kicad_pcb, usainbot2.kicad_sch]
2022-05-30 add logos in silkscreen
    [usainbot2.kicad_pcb]
2022-06-06 updated pcb silkscreen and v3 firmware
    [usainbot2.kicad_pcb]
2022-06-07 add TB6612FNG documentation and update pcb
    [usainbot2.kicad_pcb, usainbot2.kicad_sch]
2022-08-19 nuevo archivo de definiciones de los pines del robot
2022-12-14 de agrega standby
2023-05-16 integra standby con corrección de mapeo

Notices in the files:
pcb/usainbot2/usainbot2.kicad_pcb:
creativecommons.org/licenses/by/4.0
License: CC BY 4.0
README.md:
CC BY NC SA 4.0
